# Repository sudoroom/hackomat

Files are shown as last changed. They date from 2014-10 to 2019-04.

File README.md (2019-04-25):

# hack-o-mat vending machine

* so like the triac chips we tried, none of them were good enough for the motors in the vending machine.

* MOC3021 would work once and then fail closed, running the motor forever and smoking

* FOD420 did the same thing basically, although one of them worked a few times first

* TLP3023 never worked at all, probably because they're only rated for 100mA and died instantly

* not sure what part to try next

see https://sudoroom.org/wiki/Hack-o-mat
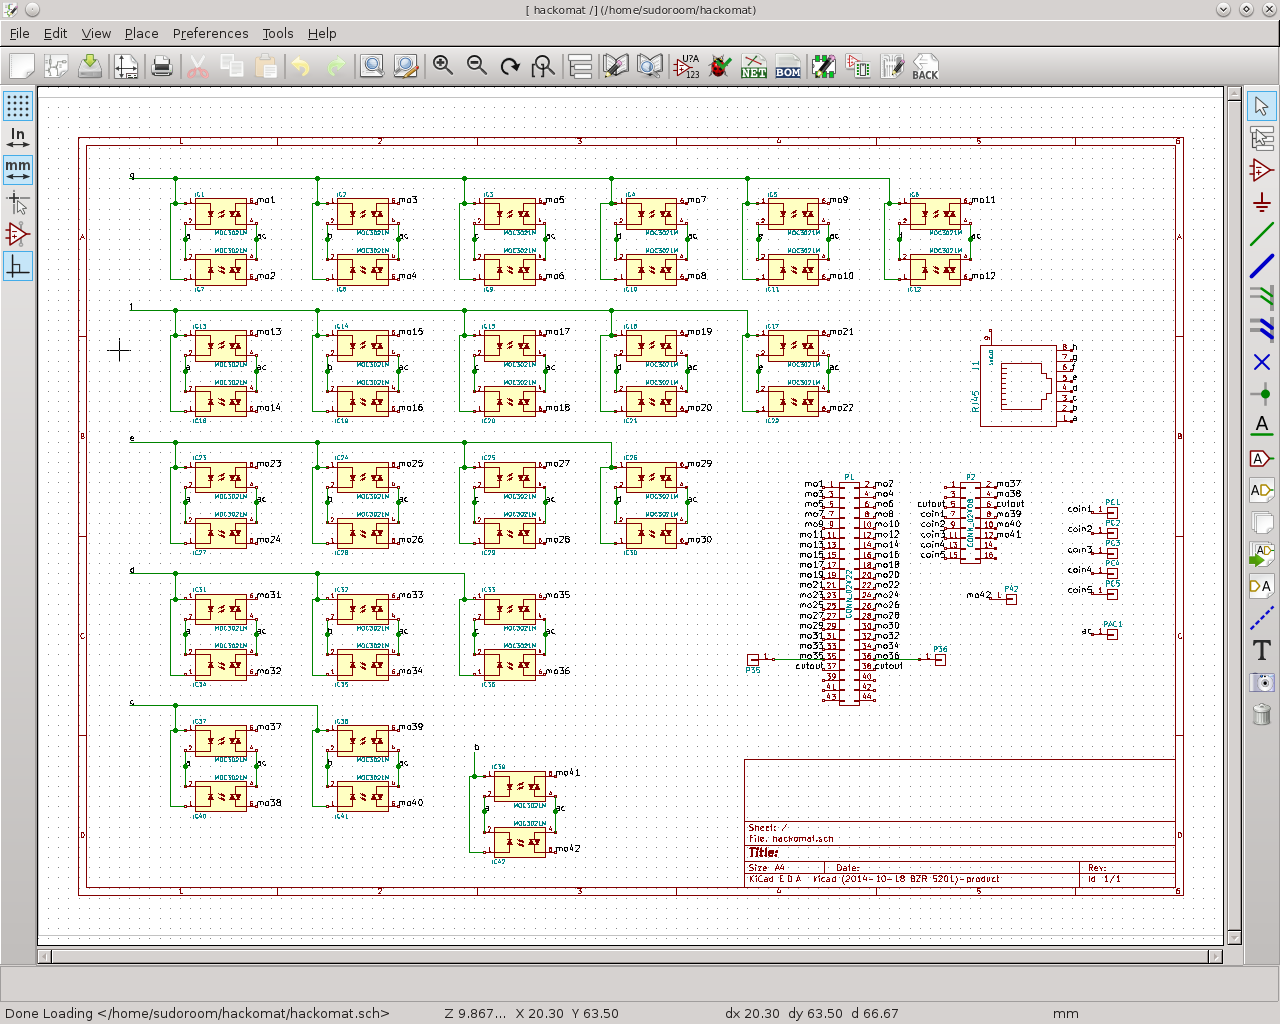
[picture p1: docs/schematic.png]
schematic

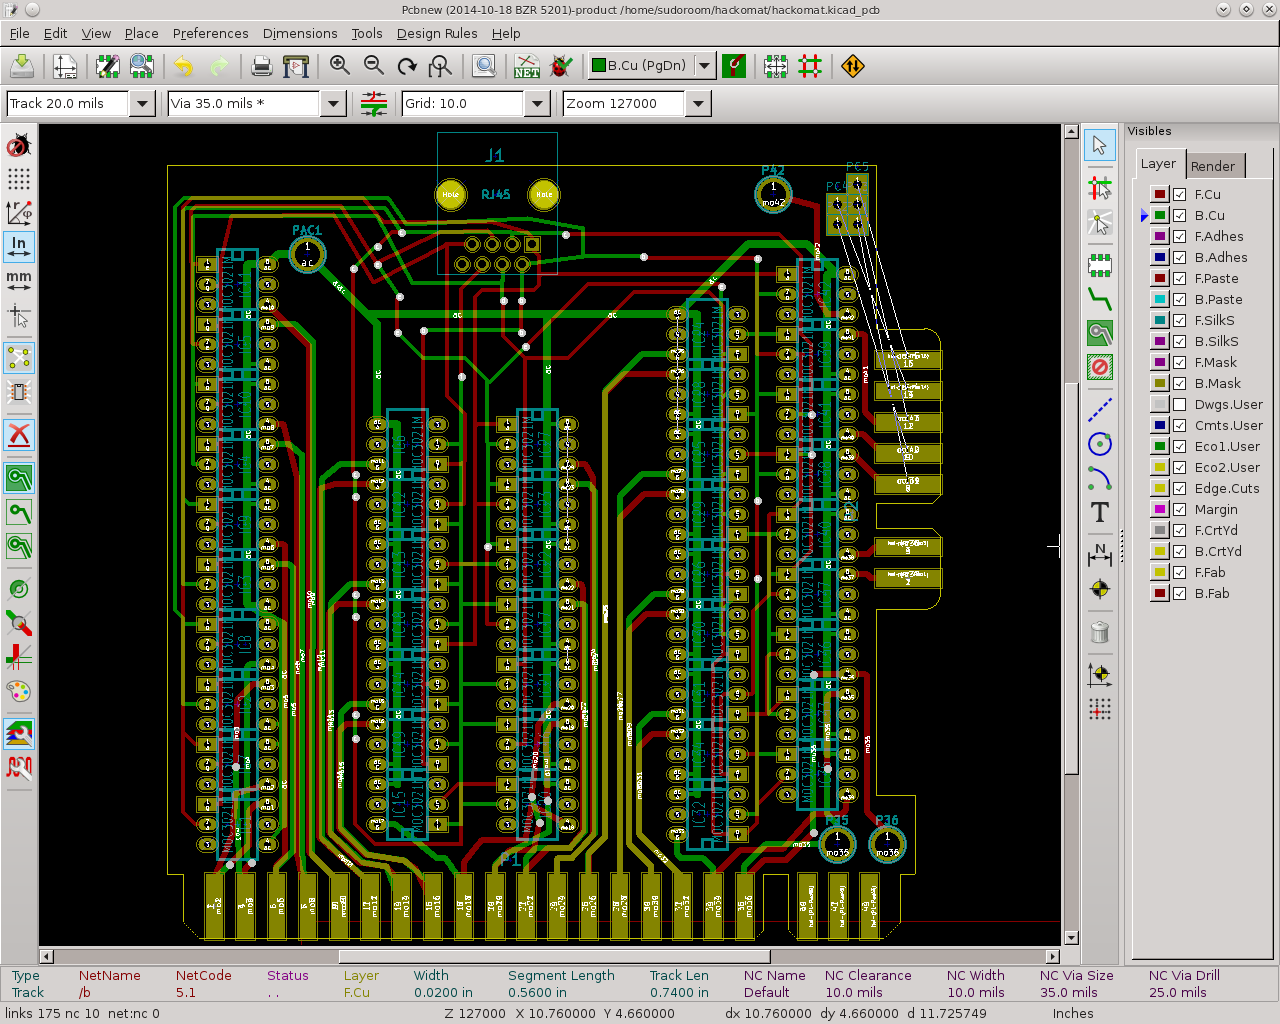
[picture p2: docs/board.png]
board


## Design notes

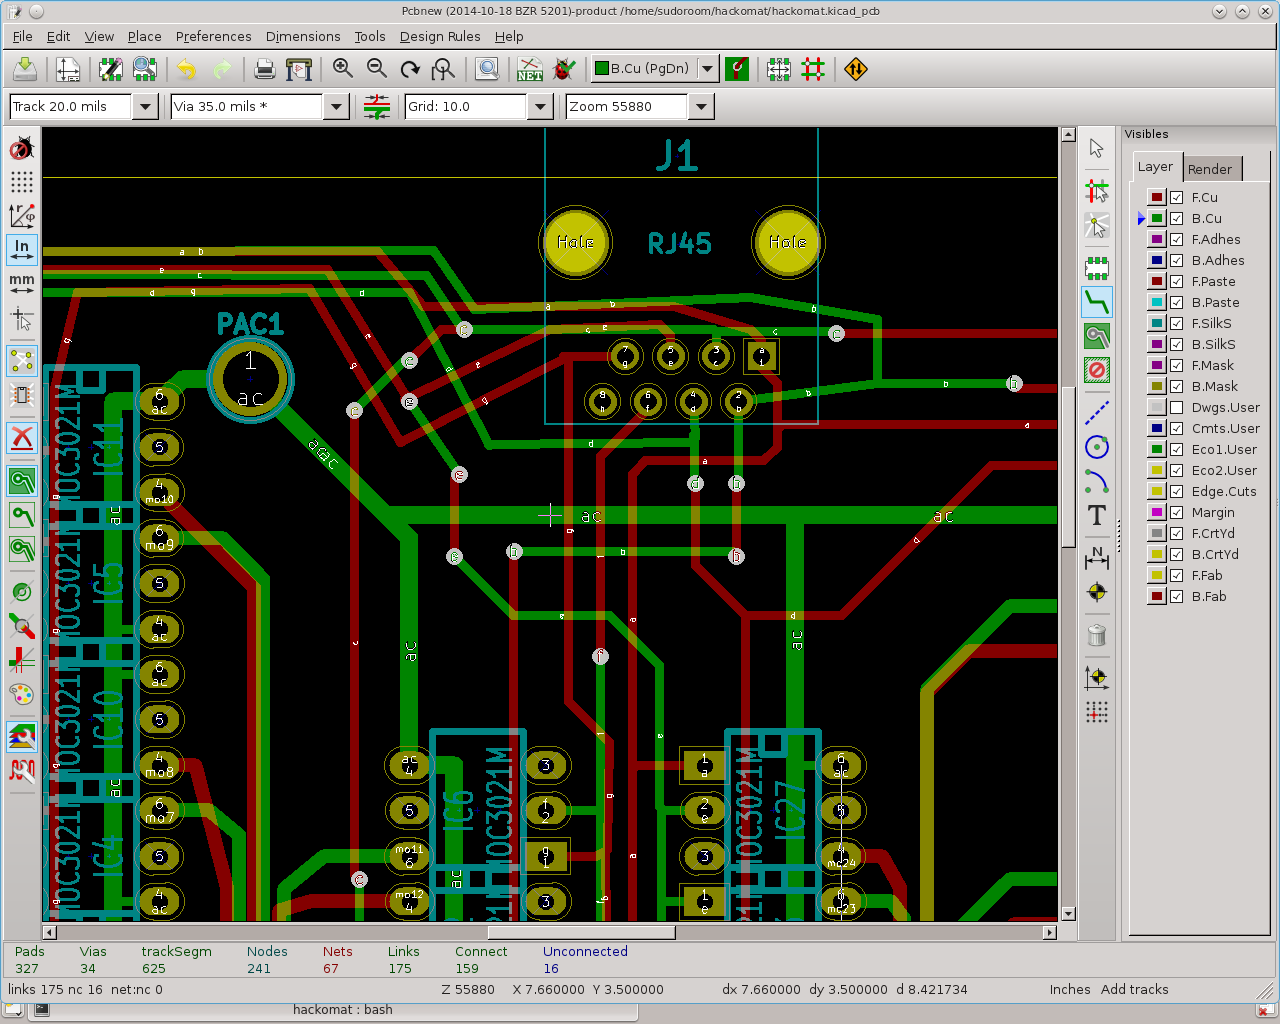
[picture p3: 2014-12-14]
docs/fun_with_vias.png

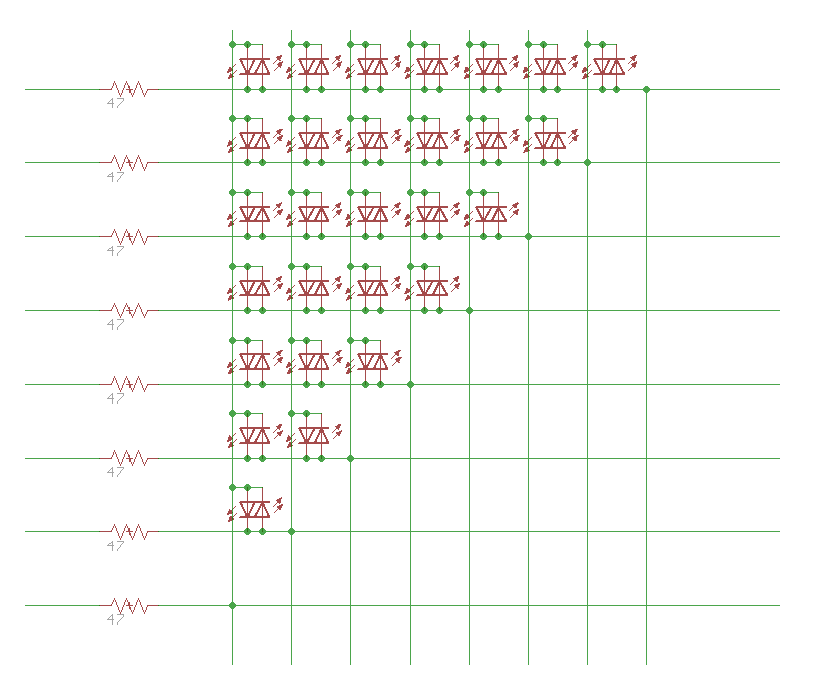
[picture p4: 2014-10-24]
docs/Charlieplex4.png

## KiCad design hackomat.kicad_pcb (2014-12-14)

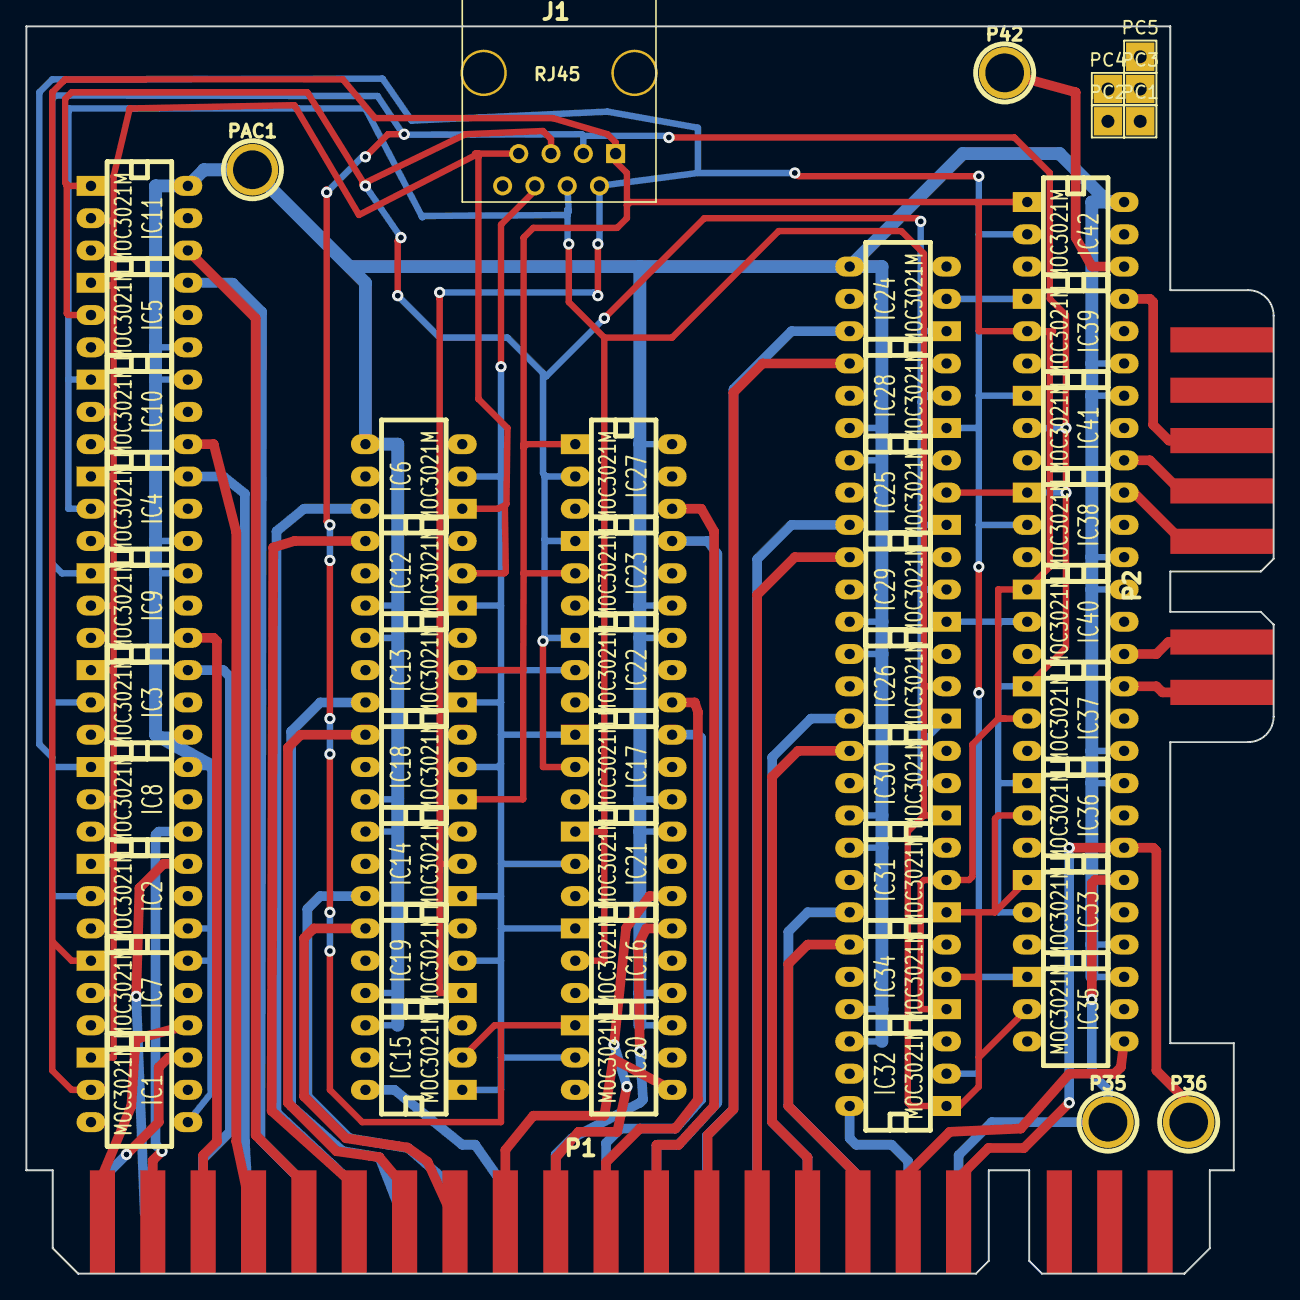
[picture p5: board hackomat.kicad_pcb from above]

Board: 2 copper layers, 98.1 x 98.1 mm, 54 parts (0 on the bottom side), 55 nets.

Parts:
IC1, IC2, IC3, IC4, IC5, IC6, IC7, IC8, IC9, IC10, IC11, IC12, IC13, IC14, IC15, IC16, IC17, IC18, IC19, IC20, IC21, IC22, IC23, IC24, IC25, IC26, IC27, IC28, IC29, IC30, IC31, IC32, IC33, IC34, IC35, IC36, IC37, IC38, IC39, IC40, IC41, IC42: MOC3021M; DIP-6__300_ELL
J1: RJ45; RJ45_8
P1: CONN_02X22; euro44
P2: CONN_02X08; euro16
P35, P36, P42: CONN_01X01; 1pin
PAC1: CONN_01X01; 1pin
PC1, PC2, PC3, PC4, PC5: CONN_01X01; Pin_Header_Straight_1x01

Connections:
/a: IC1.2, IC7.1, IC13.2, IC18.1, IC23.2, IC27.1, IC31.2, IC34.1, IC37.2, IC39.2, IC40.1, IC42.1, J1.1
/ac: IC1.4, IC2.4, IC3.4, IC4.4, IC5.4, IC6.4, IC7.6, IC8.6, IC9.6, IC10.6, IC11.6, IC12.6, IC13.4, IC14.4, IC15.4, IC16.4, IC17.4, IC18.6, IC19.6, IC20.6, IC21.6, IC22.6, IC23.4, IC24.4, IC25.4, IC26.4, IC27.6, IC28.6, IC29.6, IC30.6, IC31.4, IC32.4, IC33.4, IC34.6, IC35.6, IC36.6, IC37.4, IC38.4, IC39.4, IC40.6, IC41.6, IC42.6, PAC1.1
/b: IC2.2, IC8.1, IC14.2, IC19.1, IC24.2, IC28.1, IC32.2, IC35.1, IC38.2, IC39.1, IC41.1, IC42.2, J1.2
/c: IC3.2, IC9.1, IC15.2, IC20.1, IC25.2, IC29.1, IC33.2, IC36.1, IC37.1, IC38.1, IC40.2, IC41.2, J1.3
/coin1: P2.7, PC1.1
/coin2: P2.9, PC2.1
/coin3: P2.11, PC3.1
/coin4: P2.13, PC4.1
/coin5: P2.15, PC5.1
/d: IC4.2, IC10.1, IC16.2, IC21.1, IC26.2, IC30.1, IC31.1, IC32.1, IC33.1, IC34.2, IC35.2, IC36.2, J1.4
/e: IC5.2, IC11.1, IC17.2, IC22.1, IC23.1, IC24.1, IC25.1, IC26.1, IC27.2, IC28.2, IC29.2, IC30.2, J1.5
/f: IC6.2, IC12.1, IC13.1, IC14.1, IC15.1, IC16.1, IC17.1, IC18.2, IC19.2, IC20.2, IC21.2, IC22.2, J1.6
/g: IC1.1, IC2.1, IC3.1, IC4.1, IC5.1, IC6.1, IC7.2, IC8.2, IC9.2, IC10.2, IC11.2, IC12.2, J1.7
/mo1: IC1.6, P1.1
/mo2: IC7.4, P1.2
/mo3: IC2.6, P1.3
/mo4: IC8.4, P1.4
/mo5: IC3.6, P1.5
/mo6: IC9.4, P1.6
/mo7: IC4.6, P1.7
/mo8: IC10.4, P1.8
/mo9: IC5.6, P1.9
/mo10: IC11.4, P1.10
/mo11: IC6.6, P1.11
/mo12: IC12.4, P1.12
/mo13: IC13.6, P1.13
/mo14: IC18.4, P1.14
/mo15: IC14.6, P1.15
/mo16: IC19.4, P1.16
/mo17: IC15.6, P1.17
/mo18: IC20.4, P1.18
/mo19: IC16.6, P1.19
/mo20: IC21.4, P1.20
/mo21: IC17.6, P1.21
/mo22: IC22.4, P1.22
/mo23: IC23.6, P1.23
/mo24: IC27.4, P1.24
/mo25: IC24.6, P1.25
/mo26: IC28.4, P1.26
/mo27: IC25.6, P1.27
/mo28: IC29.4, P1.28
/mo29: IC26.6, P1.29
/mo30: IC30.4, P1.30
/mo31: IC31.6, P1.31
/mo32: IC34.4, P1.32
/mo33: IC32.6, P1.33
/mo34: IC35.4, P1.34
/mo35: IC33.6, P1.35, P35.1
/mo36: IC36.4, P1.36, P36.1
/mo37: IC37.6, P2.2
/mo38: IC40.4, P2.4
/mo39: IC38.6, P2.8
/mo40: IC41.4, P2.10
/mo41: IC39.6, P2.12
/mo42: IC42.4, P42.1

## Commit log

2014-10-24 first commit of hackomat triac board
    [hackomat.sch]
2014-10-24 make each triac have its own unique label on its leg
    [hackomat.sch]
2014-10-24 add connectors and pins
    [hackomat.sch]
2014-10-24 add example board-edge connector and a 44pin library symbol
2014-10-24 add schematic screenshot and README.md
2014-10-27 flipped over half the triacs since they never should have been flipped in the first place
    [hackomat.sch]
2014-11-11 add euro connectors
2014-11-11 add project folder as footprints location
2014-11-11 set footprints for connectors in schematic
    [hackomat.sch]
2014-11-11 put rounded corners onto euro16 connector
2014-12-11 cut corners and added line end notes to euro44
2014-12-11 change board edge lines from layer F.SilkS to Edge.Cuts on euro44
2014-12-11 add pcboard with connectors and edges in place
    [hackomat.kicad_pcb]
2014-12-11 move edge connectors to make entire board under 100x100mm
    [hackomat.kicad_pcb]
2014-12-11 change PC1-PC5 to have smaller pinhole footprints
    [hackomat.sch]
2014-12-11 place all triacs and other parts on board in order
    [hackomat.kicad_pcb]
2014-12-11 add image of unwired board
2014-12-11 move triacs to a more sensible, more sequential arrangement
    [hackomat.kicad_pcb]
2014-12-13 wire up about half the AC wires to triacs
    [hackomat.kicad_pcb]
2014-12-14 almost all the rj45 data pins, all the other traces
    [hackomat.kicad_pcb]
2014-12-14 board is finished thanx to substack
    [hackomat.kicad_pcb]
2014-12-14 fixed some white lines, then rayc touched it, watch out
    [hackomat.kicad_pcb]
2015-05-09 add datasheet for 2 amp 5ma-triggered triacs
